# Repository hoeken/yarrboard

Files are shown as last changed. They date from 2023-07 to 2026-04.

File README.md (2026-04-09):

# Yarrboard

A collection of open hardware projects for automation projects on your boat.

The project is broken into a few different repositories:

* [FrothFET](https://github.com/hoeken/frothfet) - 8 Channel Digital Switching board with pwm + load monitoring
* [FrothFET Firmware](https://github.com/hoeken/frothfet-firmware) - Firmware for the FrothFET board
* [Brineomatic](https://github.com/hoeken/brineomatic) - Watermaker Controller
* [Brineomatic Firwmare](https://github.com/hoeken/brineomatic) - Firmware for the Brineomatic board
* [SendIt](https://github.com/hoeken/sendit) - 8 channel sensor multitool board
* [SendIt Firwmare](https://github.com/hoeken/sendit-firmware) - Firmware for the SendIt board
* [Yarrboard Framework](https://github.com/hoeken/YarrboardFramework) - Common framework that all the boards run on
* [SignalK Plugin](https://github.com/hoeken/signalk-yarrboard-plugin) - Plugin for SignalK integration
* [Yarrboard Client](https://github.com/hoeken/yarrboard-client) - JS client for controlling a board over websocket

## Interface

Since it is based on the esp32, the main communication method is over WiFi.  Setup, config, and control are very easy using the built-in web portal.  Just point your phone to the url of the board and you're good to go.  Typically this is http://yarrboard.local or http://yarrboard.  You can change this hostname in the settings, or use the IP address instead.

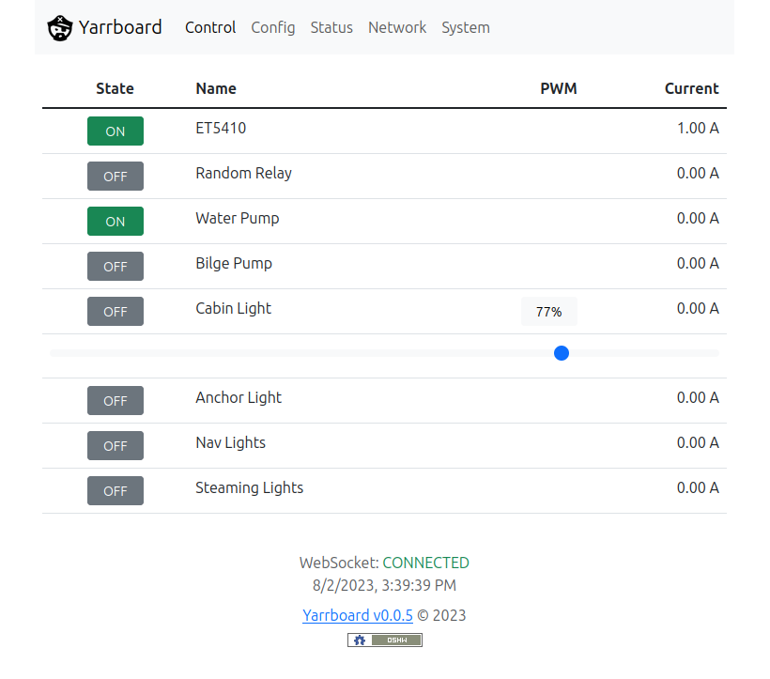
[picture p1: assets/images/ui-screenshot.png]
Screenshot of UI


## SignalK

There is also a plugin for integration with SignalK, so you can have your data all in one place.  It supports two way comms, so you can use SignalK and Node-RED to turn your loads on or off.

The plugin for SignalK is called [signalk-yarrboard-plugin](https://github.com/hoeken/signalk-yarrboard-plugin)

## How To Get One

No production as of right now, but possibly in the future.  It is 100% open source, so its possible to order PCBs, parts, and DIY your own board if you like.  There is the potential of partnering with the right person to take care of the manufacturing side of things, or you could make and sell your own - its open source after all!

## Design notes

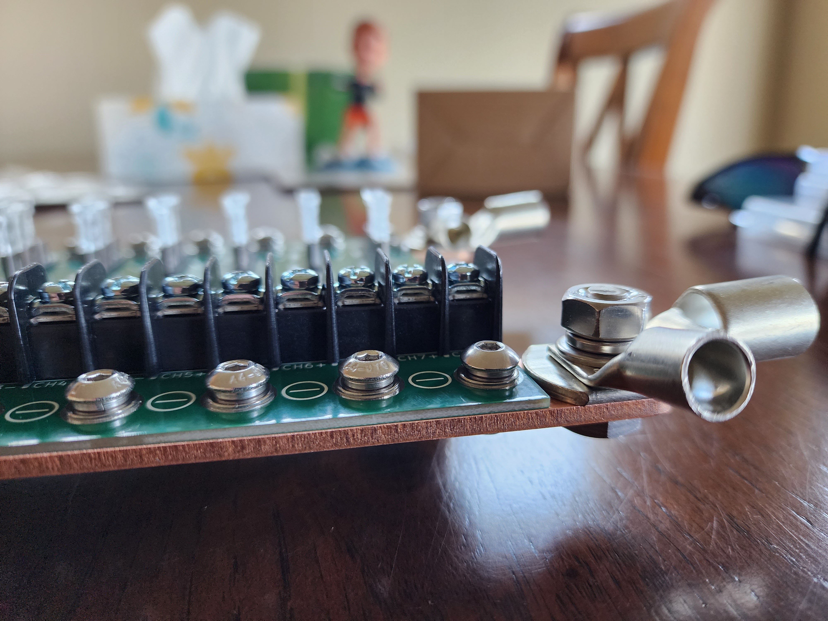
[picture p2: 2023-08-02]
assets/images/8ch-mosfet-driver-closeup.jpg

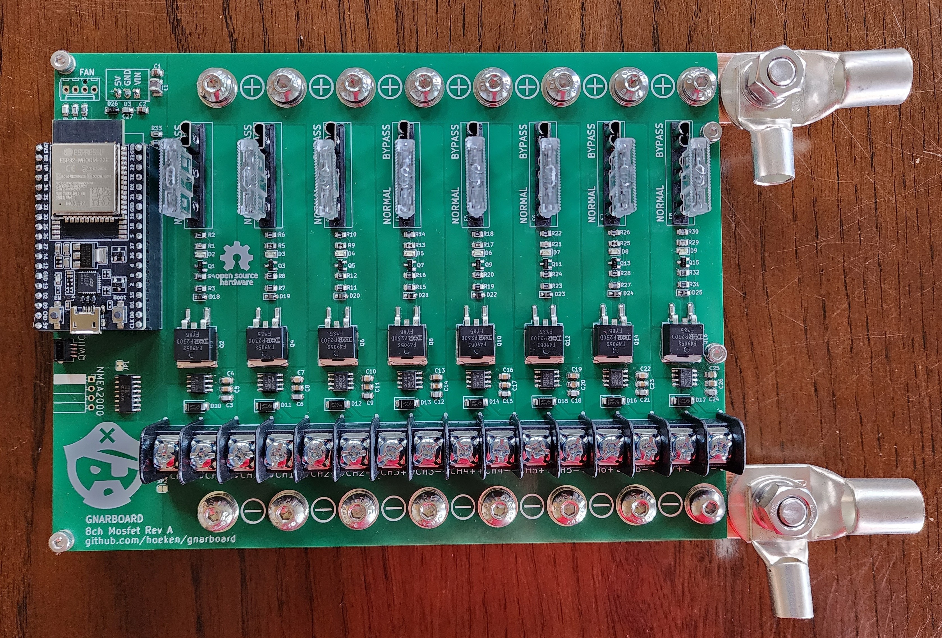
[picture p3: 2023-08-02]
assets/images/8ch-mosfet-driver.jpg

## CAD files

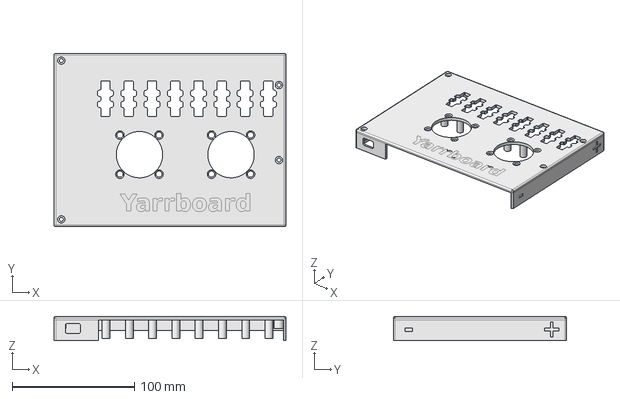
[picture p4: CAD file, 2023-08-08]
boards/8ch-mosfet/case top.FCStd
190.0 x 142.0 x 20.0 mm

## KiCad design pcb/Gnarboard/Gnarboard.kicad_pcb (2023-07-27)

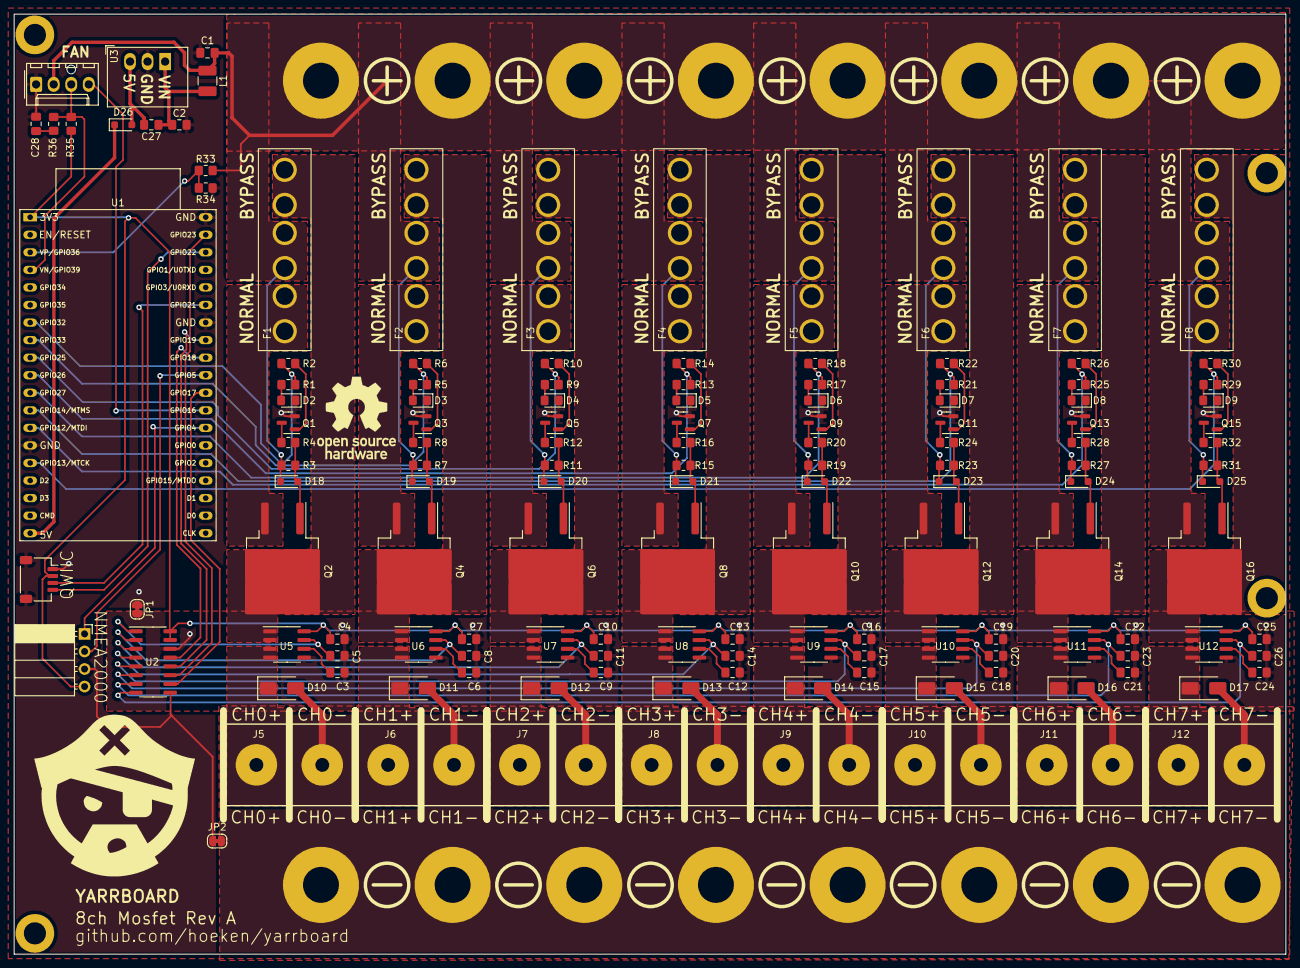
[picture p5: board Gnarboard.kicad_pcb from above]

Board: 2 copper layers, 184.0 x 136.0 mm, 140 parts (0 on the bottom side), 100 nets.

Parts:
C1, C2: 10uF; C_0805_2012Metric_Pad1.18x1.45mm_HandSolder
C3, C6, C9, C12, C15, C18, C21, C24, C27, C28: 1nF; C_0805_2012Metric_Pad1.18x1.45mm_HandSolder
C4, C7, C10, C13, C16, C19, C22, C25: 100nF; C_0805_2012Metric_Pad1.18x1.45mm_HandSolder
C5, C8, C11, C14, C17, C20, C23, C26: 4.7nF; C_0805_2012Metric_Pad1.18x1.45mm_HandSolder
D2, D3, D4, D5, D6, D7, D8, D9: LED; LED_0805_2012Metric_Pad1.15x1.40mm_HandSolder
D10, D11, D12, D13, D14, D15, D16, D17: SS16; D_SMA
D18, D19, D20, D21, D22, D23, D24, D25: 15V; D_SOD-323_HandSoldering
D26: BZX384; D_SOD-323_HandSoldering
F1, F2, F3, F4, F5, F6, F7, F8: 25A; ATC Bypass Fuse
J1: N2K; PinSocket_1x04_P2.54mm_Horizontal
J2: I2C; JST_SH_SM04B-SRSS-TB_1x04-1MP_P1.00mm_Horizontal
J3: Screw_Terminal_01x09; Busbar 1x9 .375in
J5, J6, J7, J8, J9, J10, J11, J12: Screw_Terminal_01x02; Molex 1x02 .375
JP1, JP2: SolderJumper_2_Bridged; SolderJumper-2_P1.3mm_Bridged_RoundedPad1.0x1.5mm
L1: 100uH; L_1210_3225Metric_Pad1.42x2.65mm_HandSolder
M1: Fan_4pin; Molex 0470531000
Q1, Q3, Q5, Q7, Q9, Q11, Q13, Q15: BC817; SOT-23
Q2, Q4, Q6, Q8, Q10, Q12, Q14, Q16: IRF4905; TO-263-2
R1, R5, R9, R13, R17, R21, R25, R29: 1k; R_0805_2012Metric_Pad1.20x1.40mm_HandSolder
R2, R6, R10, R14, R18, R22, R26, R30, R34, R35: 10k; R_0805_2012Metric_Pad1.20x1.40mm_HandSolder
R3, R7, R11, R15, R19, R23, R27, R31: 22k; R_0805_2012Metric_Pad1.20x1.40mm_HandSolder
R4, R8, R12, R16, R20, R24, R28, R32: 4.7k; R_0805_2012Metric_Pad1.20x1.40mm_HandSolder
R33: 100k; R_0805_2012Metric_Pad1.20x1.40mm_HandSolder
R36: 3.3k; R_0805_2012Metric_Pad1.20x1.40mm_HandSolder
U1: ESP32-DEVKITC; ESP32-DevKitC
U2: MCP3208; SOIC-16_3.9x9.9mm_P1.27mm
U3: R-78B3.3-2.0; RECOM R-78K
U5, U6, U7, U8, U9, U10, U11, U12: ACS725xLCTR-20AU; ACS7XX
locked: Screw_Terminal_01x09; Busbar 1x9 .375in

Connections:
+3.3V: C4.1, C7.1, C10.1, C13.1, C16.1, C19.1, C22.1, C25.1, J1.4, J2.2, R35.2, U1.1 (3V3), U2.15 (Vref), U2.16 (Vdd), U5.8 (VCC), U6.8 (VCC), U7.8 (VCC), U8.8 (VCC), U9.8 (VCC), U10.8 (VCC), U11.8 (VCC), U12.8 (VCC)
+5V: D26.1 (K), U1.19 (5V0)
+24V: C1.1, D18.1 (K), D19.1 (K), D20.1 (K), D21.1 (K), D22.1 (K), D23.1 (K), D24.1 (K), D25.1 (K), F1.2, F2.2, F3.2, F4.2, F5.2, F6.2, F7.2, F8.2, J3.2, J3.3, J3.4, J3.5, J3.6, J3.7, J3.8, J3.9, L1.1, M1.2 (+), R3.2, R7.2, R11.2, R15.2, R19.2, R23.2, R27.2, R31.2, R33.2
/ADC0: C5.1, U2.1 (CH0), U5.7 (VIOUT)
/ADC1: C8.1, U2.2 (CH1), U6.7 (VIOUT)
/ADC2: C11.1, U2.3 (CH2), U7.7 (VIOUT)
/ADC3: C14.1, U2.4 (CH3), U8.7 (VIOUT)
/ADC4: C17.1, U2.5 (CH4), U9.7 (VIOUT)
/ADC5: C20.1, U2.6 (CH5), U10.7 (VIOUT)
/ADC6: C23.1, U2.7 (CH6), U11.7 (VIOUT)
/ADC7: C26.1, U2.8 (CH7), U12.7 (VIOUT)
/PWM0: R1.2, R2.1, U1.7 (GPIO32)
/PWM1: R5.2, R6.1, U1.8 (GPIO33)
/PWM2: R9.2, R10.1, U1.9 (GPIO25)
/PWM3: R13.2, R14.1, U1.10 (GPIO26)
/PWM4: R17.2, R18.1, U1.11 (GPIO27)
/PWM5: R21.2, R22.1, U1.12 (GPIO14)
/PWM6: R25.2, R26.1, U1.13 (GPIO12)
/PWM7: R29.2, R30.1, U1.15 (GPIO13)
CAN_RX: J1.1, U1.26 (GPIO4)
CAN_TX: J1.2, U1.29 (GPIO5)
FAN_PWM: M1.4 (PWM), U1.27 (GPIO16)
FAN_TACHO: M1.3 (Tacho), R35.1, R36.2, U1.4 (GPIO39)
GNDA: C3.2, C4.2, C5.2, C6.2, C7.2, C8.2, C9.2, C10.2, C11.2, C12.2, C13.2, C14.2, C15.2, C16.2, C17.2, C18.2, C19.2, C20.2, C21.2, C22.2, C23.2, C24.2, C25.2, C26.2, JP1.2 (B), U2.14 (AGND), U5.5 (GND), U6.5 (GND), U7.5 (GND), U8.5 (GND), U9.5 (GND), U10.5 (GND), U11.5 (GND), U12.5 (GND)
GNDD: C1.2, C2.2, C28.2, D2.1 (K), D3.1 (K), D4.1 (K), D5.1 (K), D6.1 (K), D7.1 (K), D8.1 (K), D9.1 (K), J1.3, J2.1, J2.MP (MountPin), JP1.1 (A), JP2.2 (B), M1.1 (-), Q1.2 (E), Q3.2 (E), Q5.2 (E), Q7.2 (E), Q9.2 (E), Q11.2 (E), Q13.2 (E), Q15.2 (E), R34.1, U1.14 (GND), U1.32 (GND), U1.38 (GND), U2.9 (DGND), U3.2 (GND)
GNDPWR: D10.2 (A), D11.2 (A), D12.2 (A), D13.2 (A), D14.2 (A), D15.2 (A), D16.2 (A), D17.2 (A), J5.2, J6.2, J7.2, J8.2, J9.2, J10.2, J11.2, J12.2, JP2.1 (A), locked.2, locked.3, locked.4, locked.5, locked.6, locked.7, locked.8, locked.9
unnamed: C28.1, R36.1
unnamed: D2.2 (A), R1.1
unnamed: D3.2 (A), R5.1
unnamed: D4.2 (A), R9.1
unnamed: D5.2 (A), R13.1
unnamed: D6.2 (A), R17.1
unnamed: D7.2 (A), R21.1
unnamed: D8.2 (A), R25.1
unnamed: D9.2 (A), R29.1
unnamed: D10.1 (K), J5.1, U5.3 (IP-), U5.4 (IP-)
unnamed: D11.1 (K), J6.1, U6.3 (IP-), U6.4 (IP-)
unnamed: D12.1 (K), J7.1, U7.3 (IP-), U7.4 (IP-)
unnamed: D13.1 (K), J8.1, U8.3 (IP-), U8.4 (IP-)
unnamed: D14.1 (K), J9.1, U9.3 (IP-), U9.4 (IP-)
unnamed: D15.1 (K), J10.1, U10.3 (IP-), U10.4 (IP-)
unnamed: D16.1 (K), J11.1, U11.3 (IP-), U11.4 (IP-)
unnamed: D17.1 (K), J12.1, U12.3 (IP-), U12.4 (IP-)
unnamed: D18.2 (A), Q2.1 (G), R3.1, R4.2
unnamed: D19.2 (A), Q4.1 (G), R7.1, R8.2
unnamed: D20.2 (A), Q6.1 (G), R11.1, R12.2
unnamed: D21.2 (A), Q8.1 (G), R15.1, R16.2
unnamed: D22.2 (A), Q10.1 (G), R19.1, R20.2
unnamed: D23.2 (A), Q12.1 (G), R23.1, R24.2
unnamed: D24.2 (A), Q14.1 (G), R27.1, R28.2
unnamed: D25.2 (A), Q16.1 (G), R31.1, R32.2
unnamed: C27.2, D26.2 (A), U3.3 (OUT)
unnamed: Q1.1 (B), R2.2
unnamed: Q1.3 (C), R4.1
unnamed: F1.3, Q2.2 (D), U5.1 (IP+), U5.2 (IP+)
unnamed: F1.1, Q2.3 (S)
unnamed: Q3.1 (B), R6.2
unnamed: Q3.3 (C), R8.1
unnamed: F2.3, Q4.2 (D), U6.1 (IP+), U6.2 (IP+)
unnamed: F2.1, Q4.3 (S)
unnamed: Q5.1 (B), R10.2
unnamed: Q5.3 (C), R12.1
unnamed: F3.3, Q6.2 (D), U7.1 (IP+), U7.2 (IP+)
unnamed: F3.1, Q6.3 (S)
unnamed: Q7.1 (B), R14.2
unnamed: Q7.3 (C), R16.1
unnamed: F4.3, Q8.2 (D), U8.1 (IP+), U8.2 (IP+)
unnamed: F4.1, Q8.3 (S)
unnamed: Q9.1 (B), R18.2
unnamed: Q9.3 (C), R20.1
unnamed: F5.3, Q10.2 (D), U9.1 (IP+), U9.2 (IP+)
unnamed: F5.1, Q10.3 (S)
unnamed: Q11.1 (B), R22.2
unnamed: Q11.3 (C), R24.1
unnamed: F6.3, Q12.2 (D), U10.1 (IP+), U10.2 (IP+)
unnamed: F6.1, Q12.3 (S)
unnamed: Q13.1 (B), R26.2
unnamed: Q13.3 (C), R28.1
unnamed: F7.3, Q14.2 (D), U11.1 (IP+), U11.2 (IP+)
unnamed: F7.1, Q14.3 (S)
unnamed: Q15.1 (B), R30.2
unnamed: Q15.3 (C), R32.1
unnamed: F8.3, Q16.2 (D), U12.1 (IP+), U12.2 (IP+)
unnamed: F8.1, Q16.3 (S)
unnamed: U1.28 (GPIO17), U2.10 (~CS/SHDN)
unnamed: U1.30 (GPIO18), U2.13 (CLK)
unnamed: U1.31 (GPIO19), U2.12 (Dout)
unnamed: U1.37 (GPIO23), U2.11 (Din)
unnamed: R33.1, R34.2, U1.3 (GPIO36)
unnamed: C2.1, C27.1, L1.2, U3.1 (IN)
unnamed: C3.1, U5.6 (FILTER)
unnamed: C6.1, U6.6 (FILTER)
unnamed: C9.1, U7.6 (FILTER)
unnamed: C12.1, U8.6 (FILTER)
unnamed: C15.1, U9.6 (FILTER)
unnamed: C18.1, U10.6 (FILTER)
unnamed: C21.1, U11.6 (FILTER)
unnamed: C24.1, U12.6 (FILTER)
SCL: J2.4, U1.36 (GPIO22)
SDA: J2.3, U1.33 (GPIO21)

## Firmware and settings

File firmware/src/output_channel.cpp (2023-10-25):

/*
  Yarrboard
  
  Author: Zach Hoeken <hoeken@gmail.com>
  Website: https://github.com/hoeken/yarrboard
  License: GPLv3
*/

#include "config.h"

#ifdef YB_HAS_OUTPUT_CHANNELS

#include "output_channel.h"

//the main star of the event
OutputChannel output_channels[YB_OUTPUT_CHANNEL_COUNT];

//flag for hardware fade status
static volatile bool isChannelFading[YB_FAN_COUNT];

/* Setting PWM Properties */
const int MAX_DUTY_CYCLE = (int)(pow(2, YB_OUTPUT_CHANNEL_PWM_RESOLUTION) - 1);

#ifdef YB_OUTPUT_CHANNEL_ADC_DRIVER_MCP3208
  MCP3208 _adcCurrentMCP3208;
#endif

/*
 * This callback function will be called when fade operation has ended
 * Use callback only if you are aware it is being called inside an ISR
 * Otherwise, you can use a semaphore to unblock tasks
 */
static bool cb_ledc_fade_end_event(const ledc_cb_param_t *param, void *user_arg)
{
    portBASE_TYPE taskAwoken = pdFALSE;

    if (param->event == LEDC_FADE_END_EVT) {
        isChannelFading[(int)user_arg] = false;
    }

    return (taskAwoken == pdTRUE);
}

void output_channels_setup()
{
  #ifdef YB_OUTPUT_CHANNEL_ADC_DRIVER_MCP3208
    _adcCurrentMCP3208.begin(YB_OUTPUT_CHANNEL_ADC_CS);
  #endif

  //the init here needs to be done in a specific way, otherwise it will hang or get caught in a crash loop if the board finished a fade during the last crash
  //based on this issue: https://github.com/espressif/esp-idf/issues/5167

  //intitialize our channel
  for (short i = 0; i < YB_OUTPUT_CHANNEL_COUNT; i++)
  {
    output_channels[i].id = i;
    output_channels[i].setup();
    output_channels[i].setupLedc();
  }

  //fade function
  ledc_fade_func_uninstall();
  ledc_fade_func_install(0);

  //intitialize our interrupts afterwards
  for (short i = 0; i < YB_OUTPUT_CHANNEL_COUNT; i++)
    output_channels[i].setupInterrupt();
}

void output_channels_loop()
{
  //maintenance on our channels.
  for (byte id = 0; id < YB_OUTPUT_CHANNEL_COUNT; id++)
  {
    output_channels[id].checkAmperage();
    output_channels[id].saveThrottledDutyCycle();
    output_channels[id].checkIfFadeOver();
  }
}

bool isValidOutputChannel(byte cid)
{
  if (cid < 0 || cid >= YB_OUTPUT_CHANNEL_COUNT)
    return false;
  else
    return true;
}

void OutputChannel::setup()
{
  char prefIndex[YB_PREF_KEY_LENGTH];

  //lookup our name
  sprintf(prefIndex, "pwmName%d", this->id);
  if (preferences.isKey(prefIndex))
    strlcpy(this->name, preferences.getString(prefIndex).c_str(), sizeof(this->name));
  else
    sprintf(this->name, "Channel #%d", this->id);

  //enabled or no
  sprintf(prefIndex, "pwmEnabled%d", this->id);
  if (preferences.isKey(prefIndex))
    this->isEnabled = preferences.getBool(prefIndex);
  else
    this->isEnabled = true;

  //lookup our duty cycle
  sprintf(prefIndex, "pwmDuty%d", this->id);
  if (preferences.isKey(prefIndex))
    this->dutyCycle = preferences.getFloat(prefIndex);
  else
    this->dutyCycle = 1.0;
  this->lastDutyCycle = this->dutyCycle;

  //dimmability.
  sprintf(prefIndex, "pwmDimmable%d", this->id);
  if (preferences.isKey(prefIndex))
    this->isDimmable = preferences.getBool(prefIndex);
  else
    this->isDimmable = true;

  //soft fuse
  sprintf(prefIndex, "pwmSoftFuse%d", this->id);
  if (preferences.isKey(prefIndex))
    this->softFuseAmperage = preferences.getFloat(prefIndex);
  else
    this->softFuseAmperage = YB_FAN_MAX_CHANNEL_AMPS;

  //soft fuse trip count
  sprintf(prefIndex, "pwmTripCount%d", this->id);
  if (preferences.isKey(prefIndex))
    this->softFuseTripCount = preferences.getUInt(prefIndex);
  else
    this->softFuseTripCount = 0;

  this->adcHelper = new MCP3208Helper(3.3, this->id, &_adcCurrentMCP3208);  
}

void OutputChannel::setupLedc()
{
  //deinitialize our pin.
  //ledc_fade_func_uninstall();
  ledcDetachPin(this->_pins[this->id]);

  //initialize our PWM channels
  ledcSetup(this->id, YB_OUTPUT_CHANNEL_PWM_FREQUENCY, YB_OUTPUT_CHANNEL_PWM_RESOLUTION);
  ledcAttachPin(this->_pins[this->id], this->id);
  ledcWrite(this->id, 0);
}

void OutputChannel::setupInterrupt()
{
  int channel = this->id;
  isChannelFading[this->id] = false;

  ledc_cbs_t callbacks = {
      .fade_cb = cb_ledc_fade_end_event
  };

  //this is our callback handler for fade end.
  ledc_cb_register(LEDC_HIGH_SPEED_MODE, (ledc_channel_t)channel, &callbacks, (void *)channel);
}

void OutputChannel::saveThrottledDutyCycle()
{
  //after 5 secs of no activity, we can save it.
  if (this->dutyCycleIsThrottled && millis() - this->lastDutyCycleUpdate > YB_DUTY_SAVE_TIMEOUT)
    this->setDuty(this->dutyCycle);
}

void OutputChannel::updateOutput()
{
  //what PWM do we want?
  int pwm = 0;
  if (this->isDimmable)
    pwm = this->dutyCycle * MAX_DUTY_CYCLE;
  else
    pwm = MAX_DUTY_CYCLE;

  //if its off, zero it out
  if (!this->state)
    pwm = 0;

  //if its tripped, zero it out.
  if (this->tripped)
    pwm = 0;

  //okay, set our pin state.
  if (!isChannelFading[this->id])
    ledcWrite(this->id, pwm);
}

float OutputChannel::toAmperage(float voltage)
{
  float amps = (voltage - (3.3 * 0.1)) / (0.132); //ACS725LLCTR-20AU

  //our floor is zero amps
  amps = max((float)0.0, amps);

  return amps;
}

float OutputChannel::getAmperage()
{
  return this->toAmperage(this->adcHelper->toVoltage(this->adcHelper->getReading()));
}

void OutputChannel::checkAmperage()
{
  this->amperage = this->getAmperage();
  this->checkSoftFuse();
}

void OutputChannel::checkSoftFuse()
{
  //only trip once....
  if (!this->tripped)
  {
    //Check our soft fuse, and our max limit for the board.
    if (abs(this->amperage) >= this->softFuseAmperage || abs(this->amperage) >= YB_FAN_MAX_CHANNEL_AMPS)
    {
      //TODO: maybe double check the amperage again here?

      //record some variables
      this->tripped = true;
      this->state = false;
      this->softFuseTripCount++;

      //actually shut it down!
      this->updateOutput();

      //save to our storage
      char prefIndex[YB_PREF_KEY_LENGTH];
      sprintf(prefIndex, "pwmTripCount%d", this->id);
      preferences.putUInt(prefIndex, this->softFuseTripCount);
    }
  }
}

void OutputChannel::setFade(float duty, int max_fade_time_ms)
{
  // is our earlier hardware fade over yet?
  if (!isChannelFading[this->id])
  {
    //dutyCycle is a default - will be non-zero when state is off
    if (this->state)
      this->fadeDutyCycleStart = this->dutyCycle;
    else
      this->fadeDutyCycleStart = 0.0;

    //fading turns on the channel.
    this->state = true;

    //some vars for tracking.
    isChannelFading[this->id] = true;
    this->fadeRequested = true;

    this->fadeDutyCycleEnd = duty;
    this->fadeStartTime = millis();
    this->fadeEndTime = millis() + max_fade_time_ms + 100;

    //call our hardware fader
    int target_duty = duty * MAX_DUTY_CYCLE;
    ledc_set_fade_time_and_start(LEDC_HIGH_SPEED_MODE, (ledc_channel_t)this->id, target_duty, max_fade_time_ms, LEDC_FADE_NO_WAIT);
  }
}
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

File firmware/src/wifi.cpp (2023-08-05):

/*
  Yarrboard
  
  Author: Zach Hoeken <hoeken@gmail.com>
  Website: https://github.com/hoeken/yarrboard
  License: GPLv3
*/

#include "wifi.h"
#include "prefs.h"
#include "server.h"

//for making a captive portal
// The default android DNS
IPAddress apIP(8,8,4,4);
const byte DNS_PORT = 53;
DNSServer dnsServer;

//default config info for our wifi
char wifi_ssid[YB_WIFI_SSID_LENGTH] = "Yarrboard";
char wifi_pass[YB_WIFI_PASSWORD_LENGTH] = "";
char wifi_mode[16] = "ap";
char local_hostname[YB_HOSTNAME_LENGTH] = "yarrboard";

//identify yourself!
char uuid[13];
bool is_first_boot = true;

void wifi_setup()
{
  if (preferences.isKey("local_hostname"))
    strlcpy(local_hostname, preferences.getString("local_hostname").c_str(), sizeof(local_hostname));

  //wifi login info.
  if (preferences.isKey("wifi_mode"))
  {
    is_first_boot = false;
    strlcpy(wifi_mode, preferences.getString("wifi_mode").c_str(), sizeof(wifi_mode));
    strlcpy(wifi_ssid, preferences.getString("wifi_ssid").c_str(), sizeof(wifi_ssid));
    strlcpy(wifi_pass, preferences.getString("wifi_pass").c_str(), sizeof(wifi_pass));
  }
  else
    is_first_boot = true;

  //get a unique ID for us
  byte mac[6];
  WiFi.macAddress(mac);
  sprintf(uuid, "%02X%02X%02X%02X%02X%02X", mac[0], mac[1], mac[2], mac[3], mac[4], mac[5]);
  Serial.print("UUID: ");
  Serial.println(uuid);

  //get an IP address
  setupWifi();
}

void wifi_loop()
{
  //run our dns... for AP mode
  if (!strcmp(wifi_mode, "ap"))
    dnsServer.processNextRequest();
}

void setupWifi()
{
  //some global config
  WiFi.setSleep(false);
  WiFi.setHostname(local_hostname);
  WiFi.useStaticBuffers(true);  //from: https://github.com/espressif/arduino-esp32/issues/7183
  WiFi.mode(WIFI_AP_STA);

  Serial.print("Hostname: ");
  Serial.print(local_hostname);
  Serial.println(".local");

  //which mode do we want?
  if (!strcmp(wifi_mode, "client"))
  {
    Serial.print("Client mode: ");
    Serial.print(wifi_ssid);
    Serial.print(" / ");
    Serial.println(wifi_pass);

    //try and connect
    connectToWifi(wifi_ssid, wifi_pass);
  }
  //default to AP mode.
  else
  {
    Serial.print("AP mode: ");
    Serial.print(wifi_ssid);
    Serial.print(" / ");
    Serial.println(wifi_pass);

    WiFi.softAP(wifi_ssid, wifi_pass);
    WiFi.softAPConfig(apIP, apIP, IPAddress(255, 255, 255, 0));

    Serial.print("AP IP address: ");
    Serial.println(apIP);

    // if DNSServer is started with "*" for domain name, it will reply with
    // provided IP to all DNS request
    dnsServer.start(DNS_PORT, "*", apIP);
  }

  //setup our local name.
  if (!MDNS.begin(local_hostname)) {
    Serial.println("Error starting mDNS");
    return;
  }
  MDNS.addService("http", "tcp", 80);
}

bool connectToWifi(const char * ssid, const char * pass)
{
  Serial.print("[WiFi] Connecting to ");
  Serial.println(ssid);

  WiFi.setAutoReconnect(true);
  WiFi.begin(ssid, pass);

  // How long to try for?
  int tryDelay = 500;
  int numberOfTries = 60;

  // Wait for the WiFi event
  while (true)
  {
    switch (WiFi.status())
    {
      case WL_NO_SSID_AVAIL:
        Serial.println("[WiFi] SSID not found");
        return false;
        break;
      case WL_CONNECT_FAILED:
        Serial.print("[WiFi] Failed");
        break;
      case WL_CONNECTION_LOST:
        Serial.println("[WiFi] Connection was lost");
        break;
      case WL_SCAN_COMPLETED:
        Serial.println("[WiFi] Scan is completed");
        break;
      case WL_DISCONNECTED:
        Serial.println("[WiFi] WiFi is disconnected");
        break;
      case WL_CONNECTED:
        Serial.println("[WiFi] WiFi is connected!");
        Serial.print("[WiFi] IP address: ");
        Serial.println(WiFi.localIP());
        return true;
        break;
      default:
        Serial.print("[WiFi] WiFi Status: ");
        Serial.println(WiFi.status());
        break;
    }

    //have we hit our limit?
    if(numberOfTries <= 0)
    {
      // Use disconnect function to force stop trying to connect
      WiFi.disconnect();
      return false;
    } else {
      numberOfTries--;
    }

    delay(tryDelay);
  }

  return false;
}

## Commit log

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2023-07-08 worked on part selection a bit
    [ADC chips.ods, current sense chips.ods, esp32 pin selection.ods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]
2023-07-08 more work on pin selection.
    [esp32 pin selection.ods]
2023-07-11 added some basic stuff for the mcp3208
    [ADC chips.ods]
2023-07-11 added current calculations for the different chips.
    [ADC chips.ods, current sense chips.ods]
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2023-07-11 working nicely with the mcp3208. winner.
    [ADC chips.ods]
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2023-07-12 added in websocket library doc.
    [websocket libraries.ods]
2023-07-12 bashing my head against this. works sometimes, doesnt other times.
    [ADC chips.ods]
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2023-07-15 started work on the pcb layout.
    [Gnarboard.kicad_pcb, Gnarboard.kicad_sch]
2023-07-15 a bit more progress on the design. kicad pretty decent these days.
    [Gnarboard.kicad_pcb, Gnarboard.kicad_sch]
2023-07-15 added pololu regulator. loving kicad.
    [Gnarboard.kicad_pcb, Gnarboard.kicad_sch]
2023-07-15 much progresso en schematico
    [Gnarboard.kicad_pcb, Gnarboard.kicad_sch, untitled.kicad_sch]
2023-07-15 wow, kicad hierarchical sheets... epic.
    [Gnarboard.kicad_pcb, Gnarboard.kicad_sch]
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2023-07-15 layout and outline starting to look pretty good.
    [Gnarboard.kicad_pcb]
2023-07-16 board mostly laid out.
    [Gnarboard.kicad_pcb, Gnarboard.kicad_sch, bss 2301.dxf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]
2023-07-16 board close to being ready for a prototype
    [Gnarboard.kicad_pcb, Gnarboard.kicad_sch, mosfet.kicad_sch]
2023-07-16 added the flyback diode
    [Gnarboard.kicad_pcb, mosfet.kicad_sch]
2023-07-16 added a qwiic connector
    [Gnarboard.kicad_pcb, Gnarboard.kicad_sch, mosfet.kicad_sch]
2023-07-16 bill of materials updated.
    [Gnarboard.kicad_pcb, Gnarboard.kicad_sch, mosfet.kicad_sch]
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2023-07-16 added in ip address to the site, fixed a couple minor UI bugs.
2023-07-17 got the mosfet driver circuit sorted - zener to the rescue. also added the CAN/N2K header.
    [Gnarboard.kicad_pcb, Gnarboard.kicad_sch, mosfet.kicad_sch]
2023-07-17 updated the pin selections and changed back to using a 5v regulator.
    [Gnarboard.kicad_pcb, Gnarboard.kicad_sch, esp32 pin selection.ods]
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2023-07-17 went over components again, should be ready to rock and roll!
    [Gnarboard.kicad_pcb, Gnarboard.kicad_sch, mosfet.kicad_sch]
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2023-07-18 more progress, found a nice easy regulator too.
    [Gnarboard.kicad_pcb, Gnarboard.kicad_sch, current consumption.ods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]
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2023-07-19 changed to busbar. blueseas posts are too tall. fml
    [Gnarboard.kicad_pcb, Gnarboard.kicad_sch, busbar.FCStd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]
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2023-07-19 okay fixed drcs. think its good to go.
    [Gnarboard.kicad_pcb]
2023-07-19 added a pwm fan output to the board.
    [Gnarboard.kicad_pcb, Gnarboard.kicad_sch, esp32 pin selection.ods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]
2023-07-20 library for the power regulator was wrong. oops.
    [Gnarboard.kicad_pcb, Gnarboard.kicad_sch, current sense chips.ods]
2023-07-20 added in the right footprint and 2d busbar drawing
    [busbar.dxf]
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2023-07-26 a couple various bugfixes
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2023-07-26 couple UI tweaks and hopefully a reliability fix
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2023-07-27 couple small fixes here and there
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2023-07-27 fixed firmware url
    [untitled.kicad_sch]
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2023-08-01 updated footprints, changed 5v diode, and added jumpers for fan voltage
    [8ch-mosfet.kicad_pcb, 8ch-mosfet.kicad_sch]
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2023-08-02 added a better adc for getting bus voltage
    [8ch-mosfet.kicad_pcb, 8ch-mosfet.kicad_sch, bus voltage.kicad_sch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]
2023-08-03 fixed a minor bug with mdns
    [wifi.cpp]
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2023-08-04 Update README.md
    couple fixes
2023-08-04 fixed error with fan init
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2023-08-05 a couple fixes to the fade script.
    [channel.cpp, channel.h]
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2023-08-06 pretty sure i figured out the crashing.
    [channel.cpp]
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2023-08-06 issues with hardware fade delays have been solved
    [channel.cpp]
2023-08-06 fixed a minor bug with the refactor
    [channel.cpp, channel.h]
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2023-08-08 updated terminal cover with pos and neg graphics
    [case top.FCStd, terminal cover.FCStd]
2023-08-08 added logo and fixed terminal cover neg
    [terminal cover.FCStd]
2023-08-08 fixed a minor bug and config'd amperages
    [channel.cpp, channel.h]
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2023-08-09 fixed a bug with the ADC soft fuse
    [channel.cpp]
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2023-08-09 upgraded the i2c/serial connectors + power based on the sailor hat schematic
    [8ch-mosfet.kicad_pcb, 8ch-mosfet.kicad_sch, bus voltage.kicad_sch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]
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2023-08-10 more or less placed all the stuff that needs to be placed
    [8ch-mosfet.kicad_pcb, connectors.kicad_sch, mosfet.kicad_sch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]
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2023-08-10 fixed drc errors, just silkscreen left
    [8ch-mosfet.kicad_pcb]
2023-08-10 added in reverse polarity diode to power circuit
    [8ch-mosfet.kicad_pcb, mosfet.kicad_sch, power.kicad_sch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]
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2023-08-11 fixed a part number
    [connectors.kicad_sch, mosfet.kicad_sch, pwm fan.kicad_sch]
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2023-08-12 tested the bus voltage stuff a bit more
    [8ch-mosfet.kicad_sch, adc input.kicad_sch, adc.kicad_sch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]
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2023-08-12 figured out most of the components, working on placement
    [adc input.kicad_sch, input switch.kicad_sch, led driver.kicad_sch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]
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2023-08-13 changed back to qwiic and moved it under the esp32
    [8ch-mosfet.kicad_pcb, connectors.kicad_sch, mosfet.kicad_sch]
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2023-08-13 too much routing
    [adc.kicad_sch, power.kicad_sch, rgb-input.kicad_pcb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]
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2023-10-19 damnit, messed up the sda/scl lines on the board
    [8ch-mosfet.kicad_pcb, adc.kicad_sch, mosfet.kicad_sch]
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2023-10-20 Fixed a bug where setup would hang on the reboot after a crash
    [channel.cpp, channel.h]
2023-10-24 working on routing the board rgb input board
    [button pad board.kicad_pcb]
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2023-10-26 massive channel -> pwm search and replace
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2023-10-27 damn, found an issue with my pinouts
    [esp32 pin selection.ods]
2023-10-27 fighting json bug... good state now.
    [esp32 pin selection.ods]
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2023-10-27 solved the ADC issue and found another minor one
    [adc input.kicad_sch, input switch.kicad_sch, led driver.kicad_sch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]
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2023-10-28 got to the bottom of the current measurement noise
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2023-10-28 first pass on redesign of the rgb input board
    [adc input.kicad_sch, adc.kicad_sch, input switch.kicad_sch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]
2023-10-28 new rgb input board coming along very nicely
    [adc input.kicad_sch, input switch.kicad_sch, led driver.kicad_sch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]
2023-10-29 worked on the pwm issues
    [8ch-mosfet.kicad_pcb, 8ch-mosfet.kicad_sch, pwm calculations.ods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]
2023-10-29 new rgb input board is starting to look very nice.
    [adc input.kicad_sch, adc.kicad_sch, input switch.kicad_sch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]
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2023-10-29 reannotated and did some more cleanup. almost ready
    [adc input.kicad_sch, adc.kicad_sch, input switch.kicad_sch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]
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2023-10-29 starting a redesign ahead of having parts to test. wish me luck
    [8ch-mosfet.kicad_pcb, 8ch-mosfet.kicad_sch, mosfet.kicad_sch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]
2023-10-29 worked on the new layout. hope the gate driver works
    [8ch-mosfet.kicad_pcb, mosfet.kicad_sch]
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2023-10-29 button board updated, routed, and ready to rock.
    [4x4.kicad_sch, button pad board.kicad_pcb, button pad board.kicad_sch]
2023-10-29 8 channel mosfet driver also ready for proto
    [8ch-mosfet.kicad_pcb, 8ch-mosfet.kicad_sch, adc.kicad_sch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]
2023-10-30 first commit of the 'totem pole' driver design
    [8ch-mosfet.kicad_pcb, 8ch-mosfet.kicad_sch, adc.kicad_sch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]
2023-10-30 oof, working from the wrong copy, had to redo some stuff
    [8ch-mosfet.kicad_pcb, 8ch-mosfet.kicad_sch, adc.kicad_sch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]
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2023-10-30 fixed the led / pwm issue. yay!
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2023-10-30 worked on the fans and have a plan for the fan.
    [esp32 pin selection.ods]
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2023-11-17 framerate update and some ui fixes
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2023-11-19 boards and firmware moved to their own repos.
    [4x4.kicad_sch, 8ch-mosfet.kicad_pcb, 8ch-mosfet.kicad_sch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]
